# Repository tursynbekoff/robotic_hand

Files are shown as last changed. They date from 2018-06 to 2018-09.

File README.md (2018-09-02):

# Development of an Autonomous Robotic Pick and Place Laboratory Setup for Intelligent Industrial Automation
    
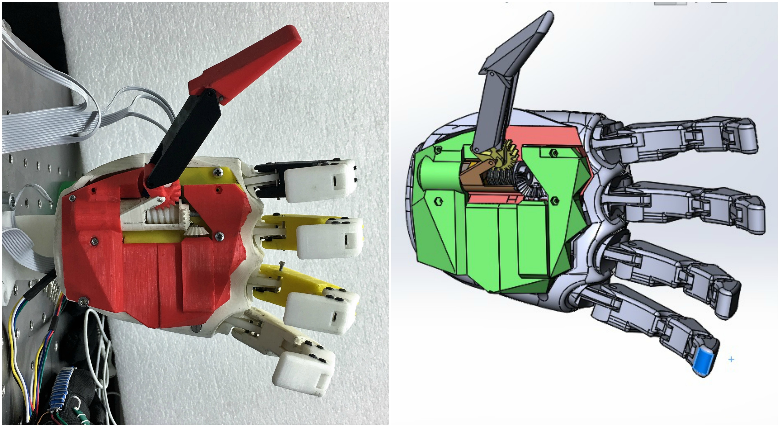
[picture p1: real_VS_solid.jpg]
 
The anthropomorphic hand consist of mechanical design and electrical components like 12V DC motor, arduino microcontroller wiring and PCB. In the following parts there will be full description of the mechanican and electrical components and source files could be found in the folders above

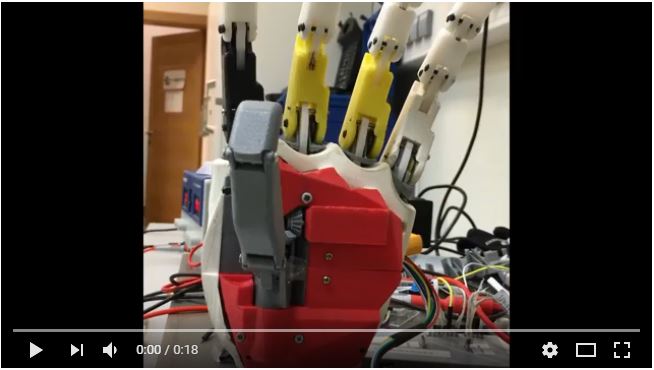
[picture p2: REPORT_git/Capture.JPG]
Video (https://youtu.be/M6sOJtzTVpo)


*  3D Design of the Hand 1.0
*  3D Design of the Hand 2.0
*  Control of the hand 

## 3D Design of the Hand 1.0
The robotic hand is still under iprovement and development stage. Here is shown previous models and developmemt steps that have been done. First model of the hand was done not by me and in a limited period of time. My goal is to improve design and eliminate problems from initial model. 

### Problems of the initial model
* Thumb was broken
* Backlash between parts 
* Wires were exposed to mechanical deformation
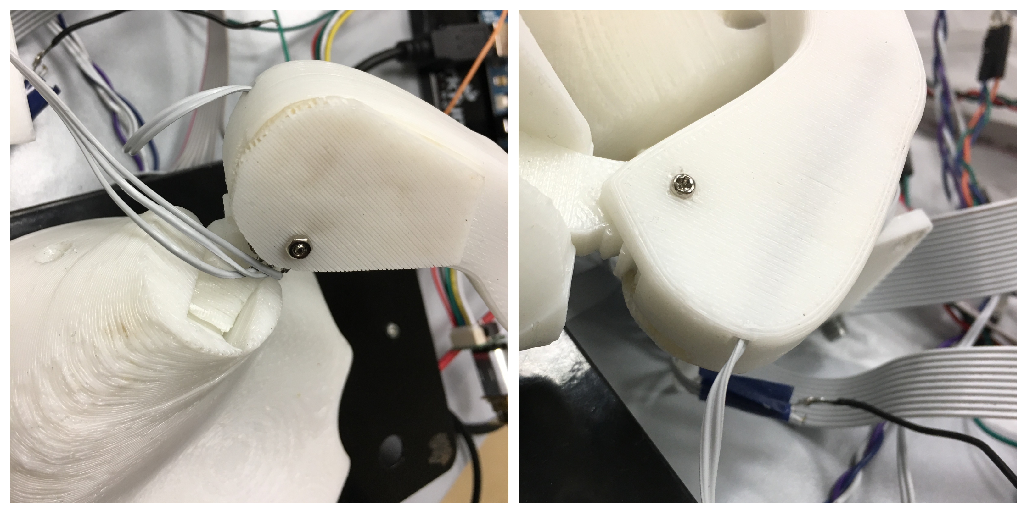
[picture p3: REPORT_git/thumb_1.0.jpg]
 
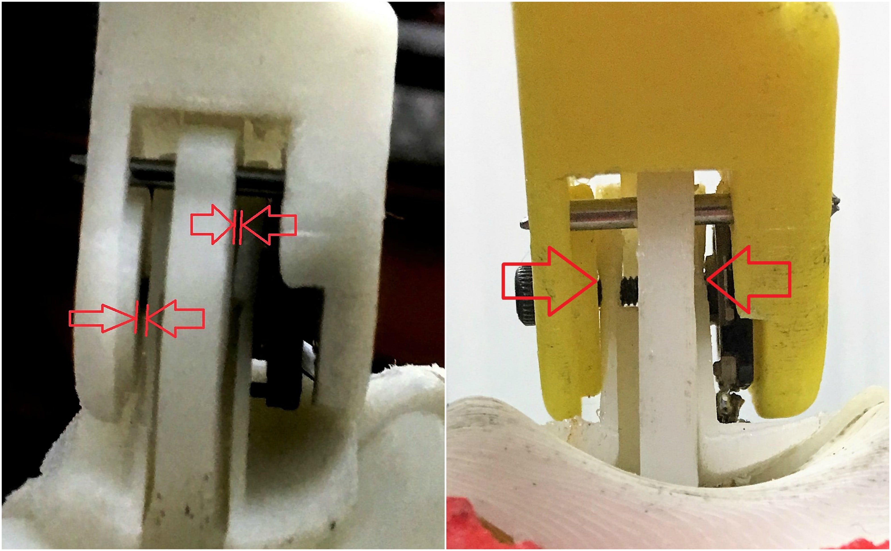
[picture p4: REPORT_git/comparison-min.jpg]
 
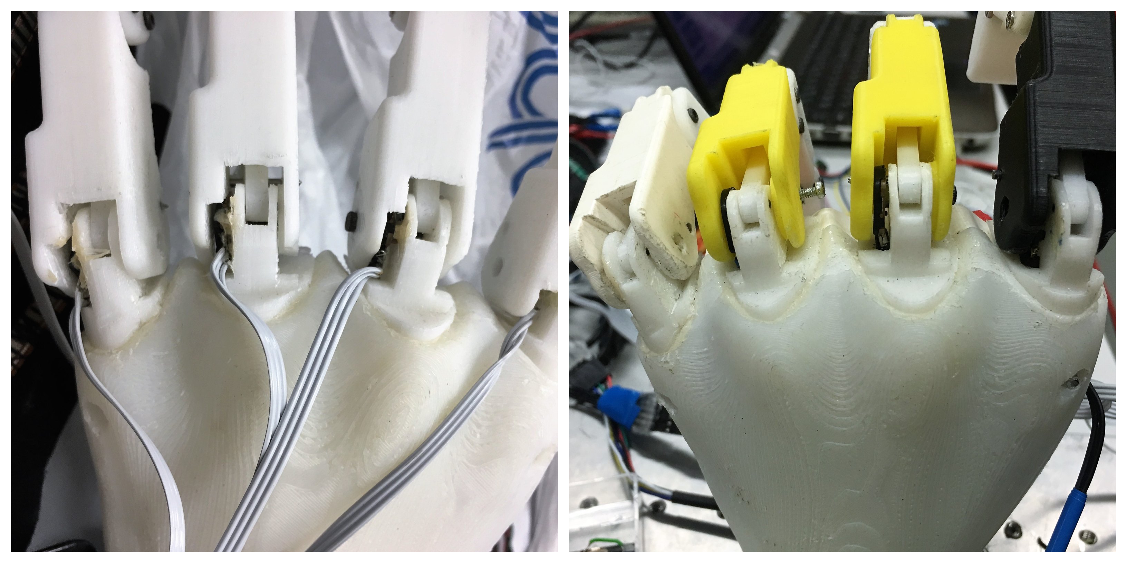
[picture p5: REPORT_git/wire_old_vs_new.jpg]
 
 
The problem with backlash was solved by replacing old parts with new ones. The new design of the "proximal phalanges" of the hand allowed to decrease backlash and the new placement of position sensors and location of the wiring of the sensors inside the hand improved sensor readings and precision of the hand. The advantage of placing position sensor inside the finger is straighforward, the data readings from sensor are cleaner and new placement also secures wiring from mechanical exposure.
### Setps of development of the new design of the thumb

The first picture demostrates initial design of the thumb

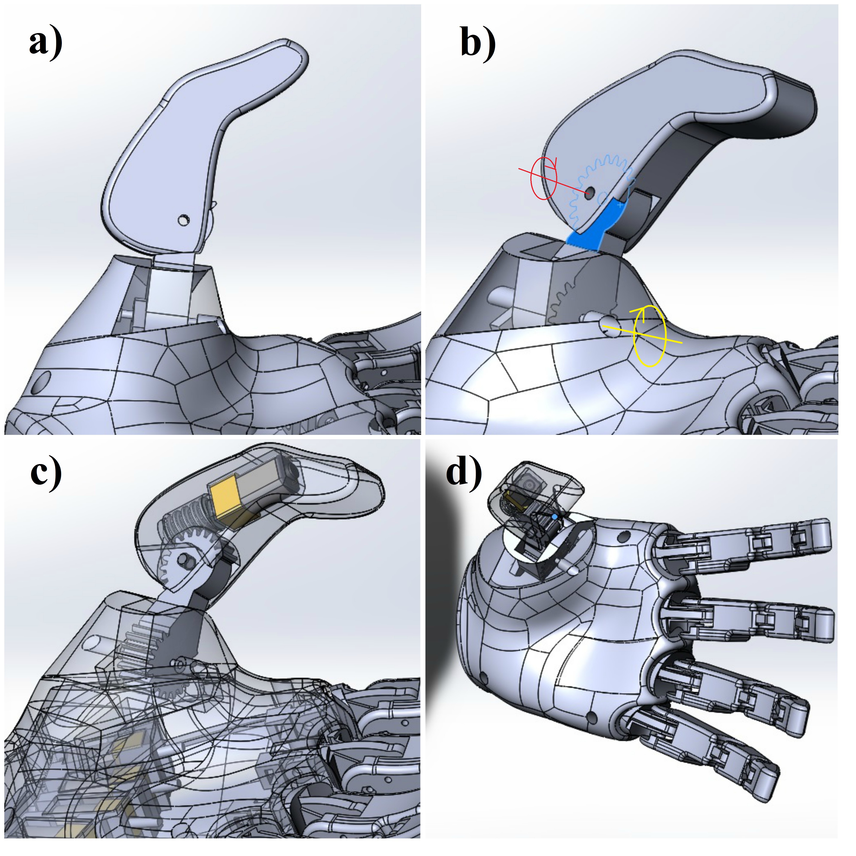
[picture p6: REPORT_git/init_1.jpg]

The first updated design of the thumb consisted from following configuration: flexion mechanism is performed with aid of brushed DC motor with integrated gearbox. The worm gear rotates spur gear which in turn performs extension, flexion movements. Moreover, the mechanism is non-backdrivable and performs in a positive way at grabbing operation it secures position even after power loss. In addition, thumb can perform underactuated adaptive closing through linkage connections. While extension, flexion operations thumb can bend depending on the placement of the object and wrap around that object. The second brushed DC motor rotates thumb with spur gear about its axis at "thumb's up" position. Thus, the thumb could perform only extension, flexion movements. However, the thumb in this configuration cannot perform abduction, adduction motions. As a result, the thumb cannot perform grabbing operation and further changes were made.

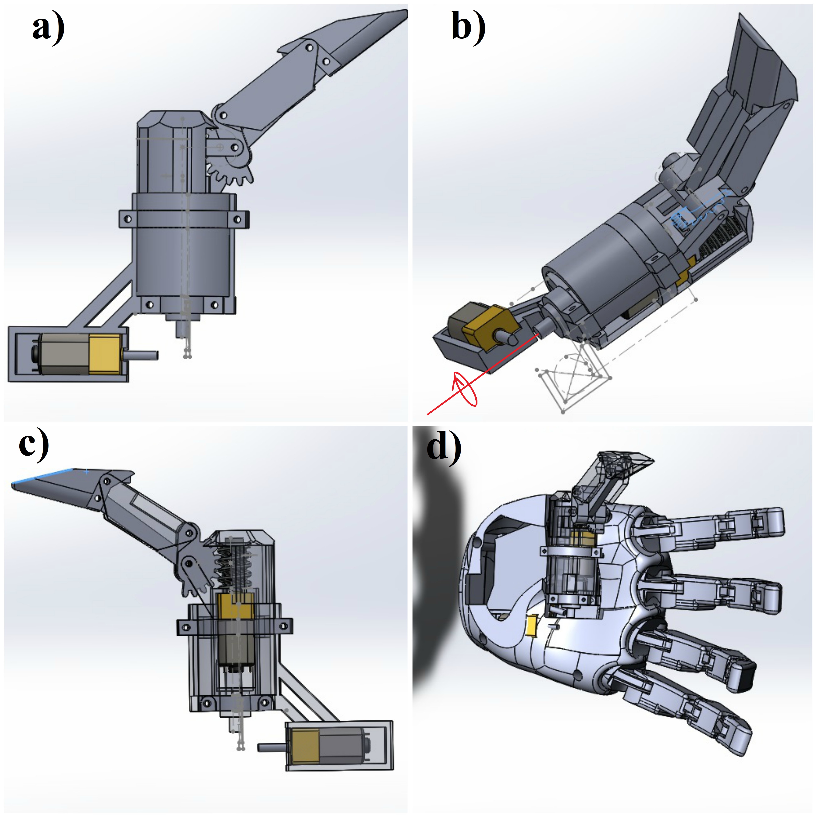
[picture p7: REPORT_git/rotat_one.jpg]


The second design of the thumb is different from initial design with the placement of the second brushed DC motor. Middle shaft were used to rotate thumb about palm plane. The thumb moves inward and outward from the palm plane, that means it can perform flexion, extension as well as abduction, adduction movements. However, this mechanism needs more space and eventually the design of the thumb were rebuilt.
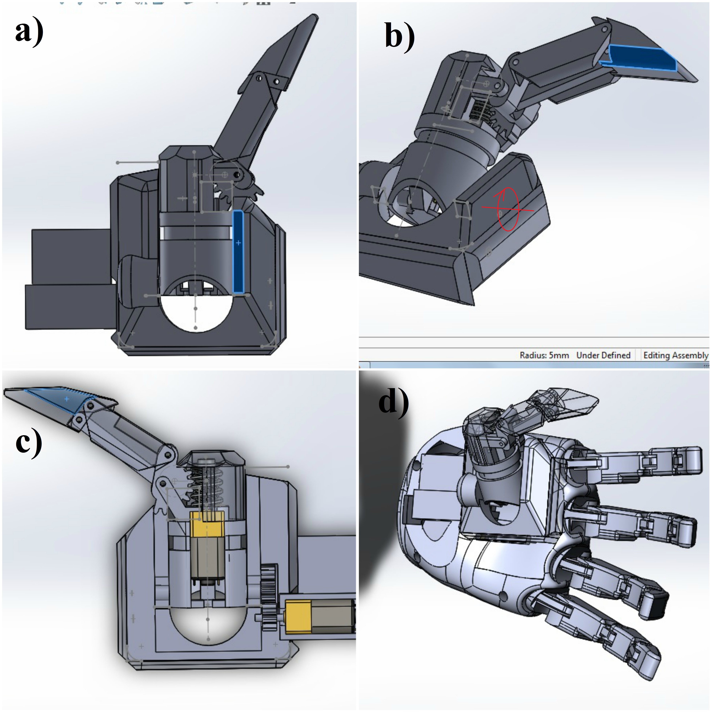
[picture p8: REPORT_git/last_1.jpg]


The next CAD model of the thumb can rotate about its base and can perform  flexion, extension and adduction. Placing the thumb opposite to index finger it can perform extension, flexion, abduction and adduction movements. In addition, this design does not need much space and can be compact in size. Space is needed only for DC motor. As a result, this CAD design is more effcient. The next design iterations  are fundamentally the same. The placement of the first DC motor is the same and adaptive mechanism is rotated to 90 degrees and placed opposite to index finger. The second brushed DC motor rotates the thumb around index finger axis by using bevel gear. The advantage using bevel gear instead of spur gear, it conserves space. As a result, we started printing the parts.

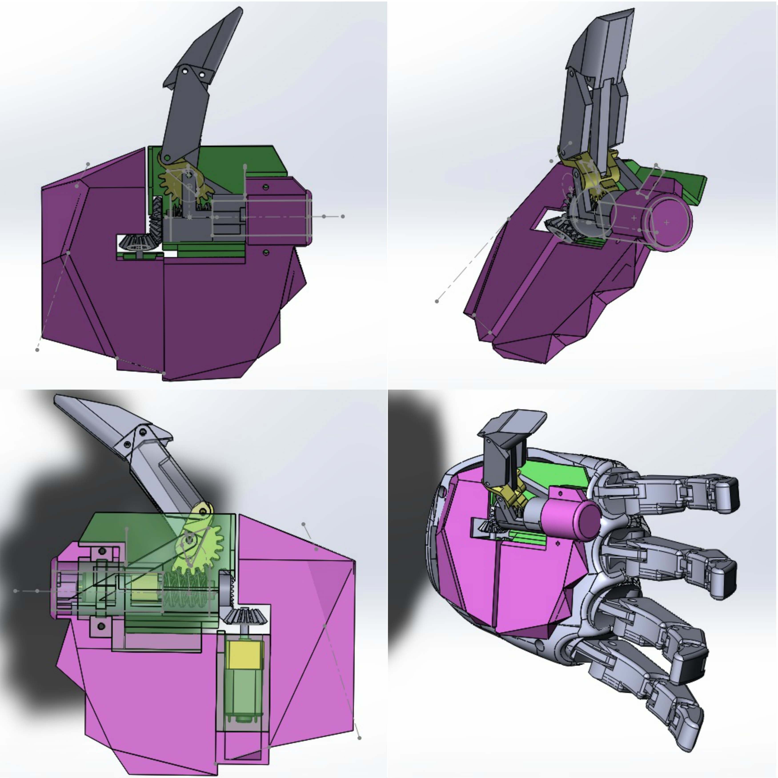
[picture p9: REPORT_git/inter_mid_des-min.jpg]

 
The last design: 

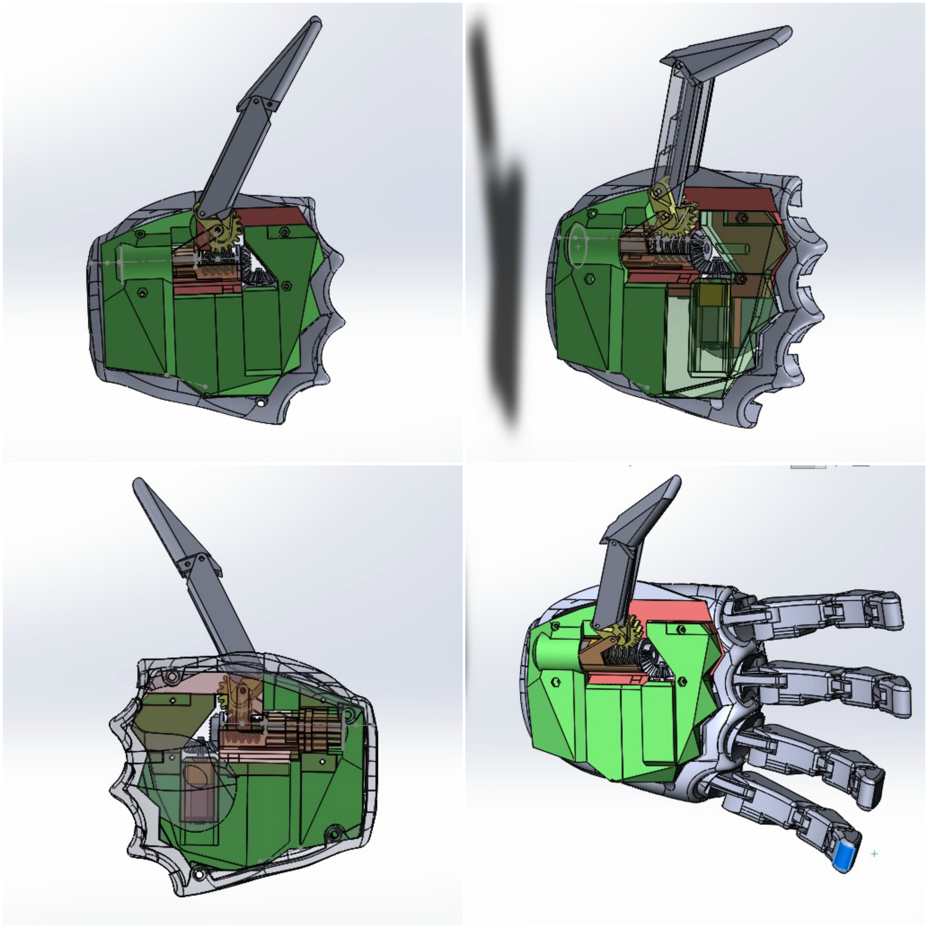
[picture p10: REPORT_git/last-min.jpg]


The next iteration was connection of mechanical part with electrical components. Due to dynamic configuration of the thumb and moving mechanical structures of the hand it created diffculties with wiring. DC motors, that were used in the project, has embedded quadratic encoders, therefore each motor has six pins to connect. The first DC motor is integrated in the moving structure that rotates around its axis. The second DC motor rotates the structure with the first DC motor. The requirement for the harness is flexibility and transmitting rated power for the motor. As a result, the wiring loom was made from copper wires that widely used in headphones. In addition, mechanical changes were made for harness wiring, it goes through narrow slot in the moving part and protected from mechanical deformation. However, the part of the wire harness which connects dynamic part with static part is exposed to bending. To secure robustness of the exposed part of the harness, insulating tape was used. 

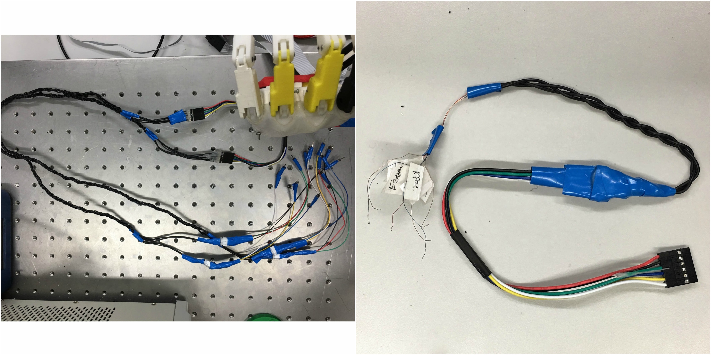
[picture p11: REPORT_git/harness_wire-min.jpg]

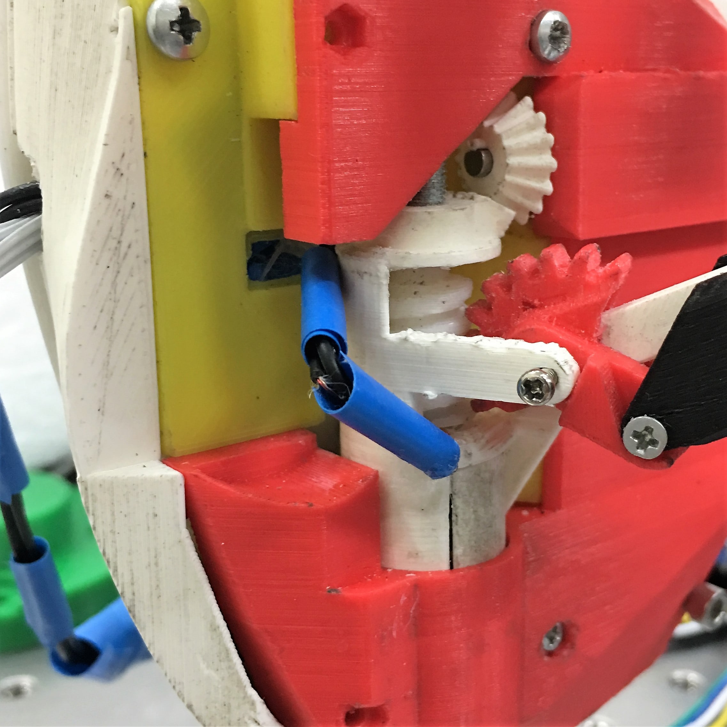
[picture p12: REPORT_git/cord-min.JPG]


As a result, the final CAD model of the thumb can perform extension, flexion and abduction, adduction movements. The main difference between initial and the final model of the thumb, it can perform under-actuated adaptive motion, which means the thumb can wrap around object with complex geometrical shape and simplifies the control of the thumb. Full up-to-date CAD model of the hand is [here](https://github.com/tursynbekoff/robotic_hand/tree/master/CAD).

### Holding objects

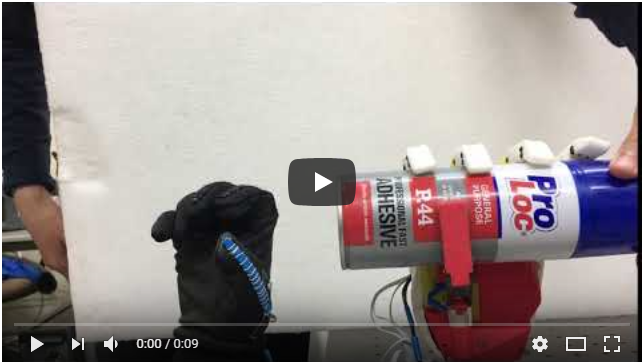
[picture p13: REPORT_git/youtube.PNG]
IMAGE ALT TEXT HERE (https://youtu.be/hmZBOrk-Xx8)


The performance of the hand with new thumb was tested with various objects. In the test
there were objects with different shapes: cylindrical, spherical and brick shaped. The hand
performed grabbing with aid of manual manipulation. The hand securely holds all objects and thumb performs adaptive gripping of the objects. Underactuated adaptive bending of the thumb helps to grab and to hold objects. However, the length and the shape of the thumb should be tuned for versatility. The grip of the thumb can be improved by adding nonbackdivable mechanism where bevel gear is placed. Other possible way to improve the grip, by resin coating on the contact point with the object, on the inner surface of the thumb.

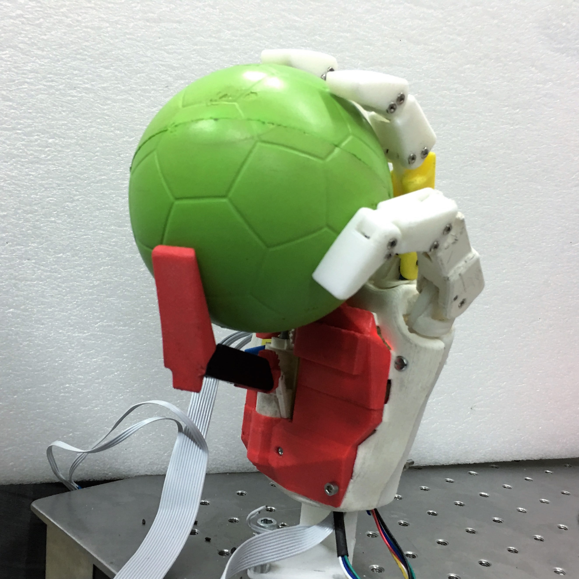
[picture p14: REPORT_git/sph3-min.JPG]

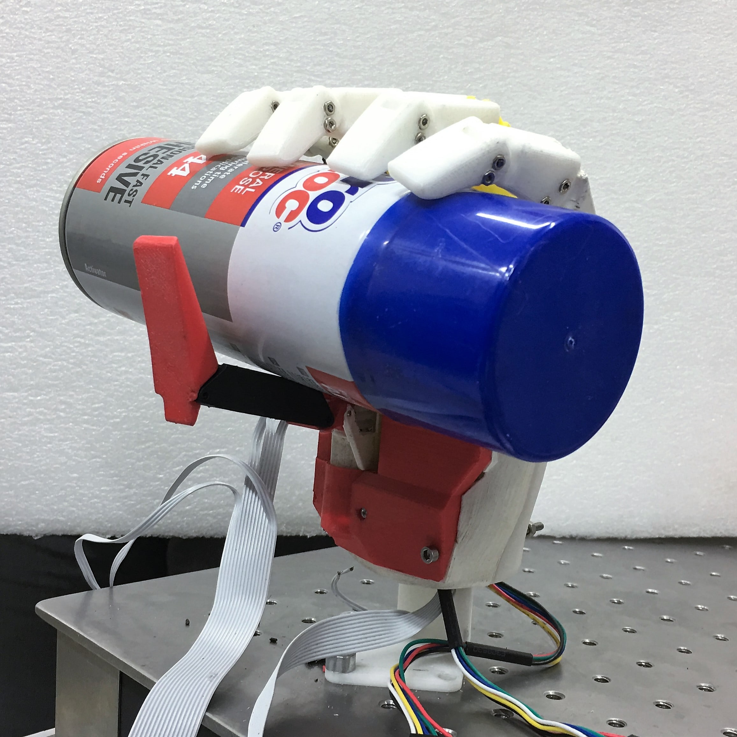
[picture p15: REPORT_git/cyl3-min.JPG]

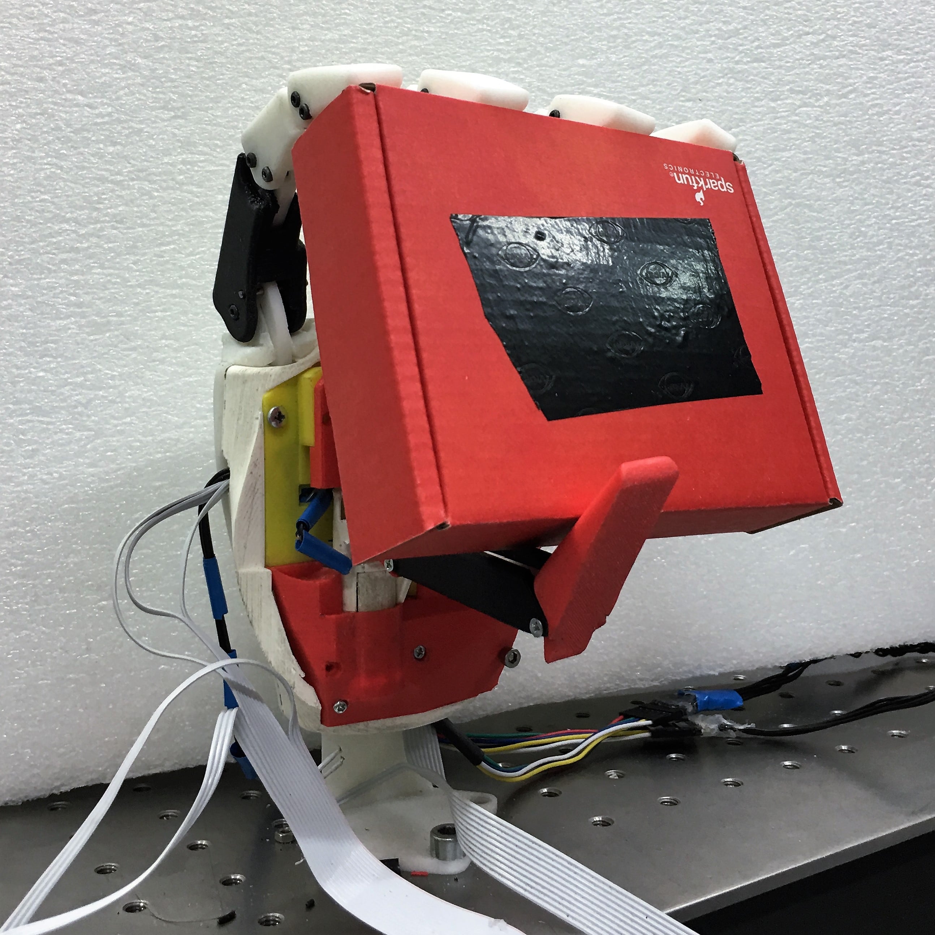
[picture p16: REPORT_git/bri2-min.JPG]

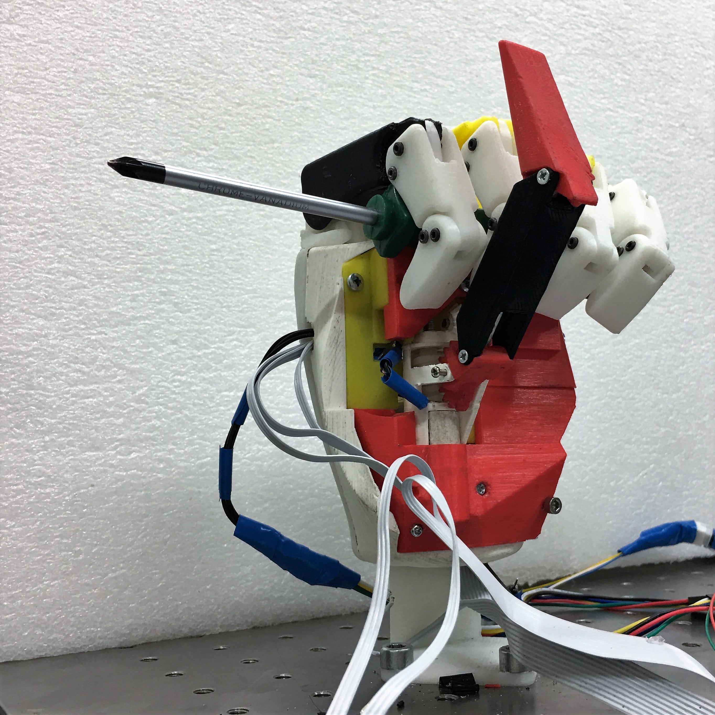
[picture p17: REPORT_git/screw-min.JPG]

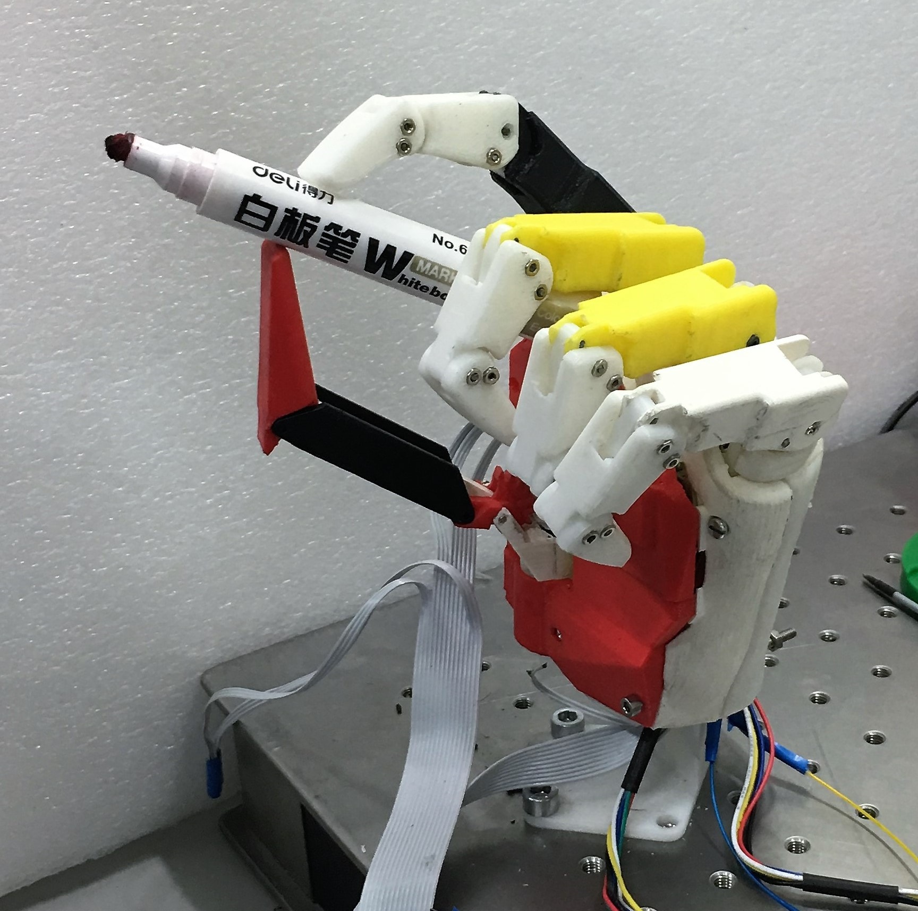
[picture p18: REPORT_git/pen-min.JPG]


In addition, household objects with complex geometrical configuration, as screwdriver, were tested. The hand can grab the objects with external manipulation and securely hold objects at specific position. The hand has potential to be used as prosthesis.

## Hand 2.0
### New Finger Mechanism
currently working on adaptive underactuated mechanism for fingers

Demo
CAD files for finger are [here](https://github.com/tursynbekoff/robotic_hand/tree/master/test_finger)

Demo

New hand with rail sysem for stablitity and robustness is under integration process.
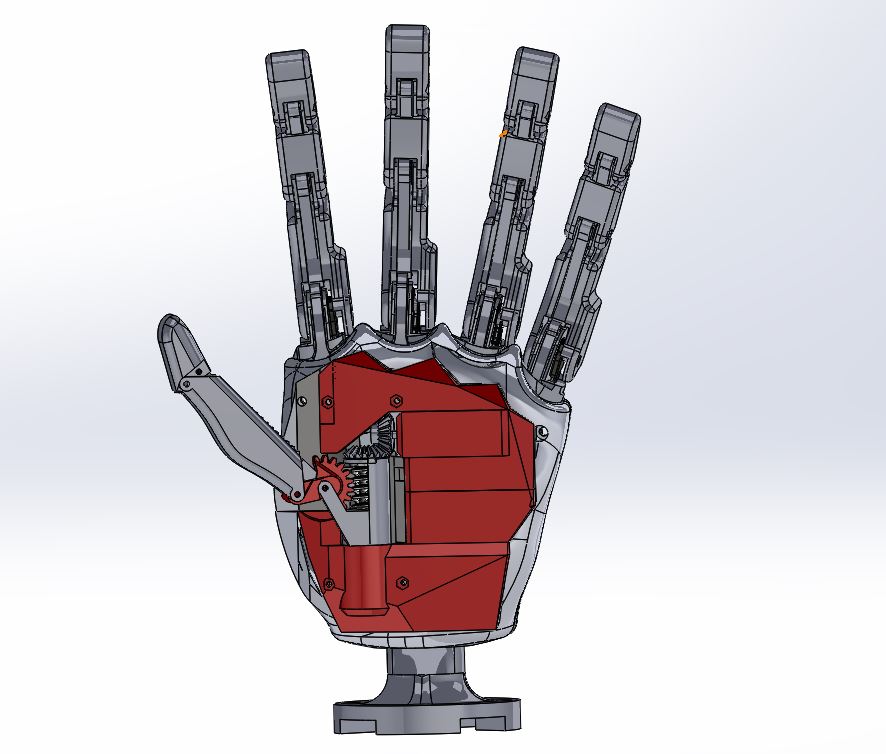
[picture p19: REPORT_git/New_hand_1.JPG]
New hand

The crossed structures are used for stiffness and strength to hold rails stable. Rails are used to navigate motor joint part durring mechanical transition from rotational motion to linear motion. Earlier there was no rail system and there were parisite vibration in rotaional motion which created disturbance in postion sensor readings. From the first tests fingers move in defined trajectory. 
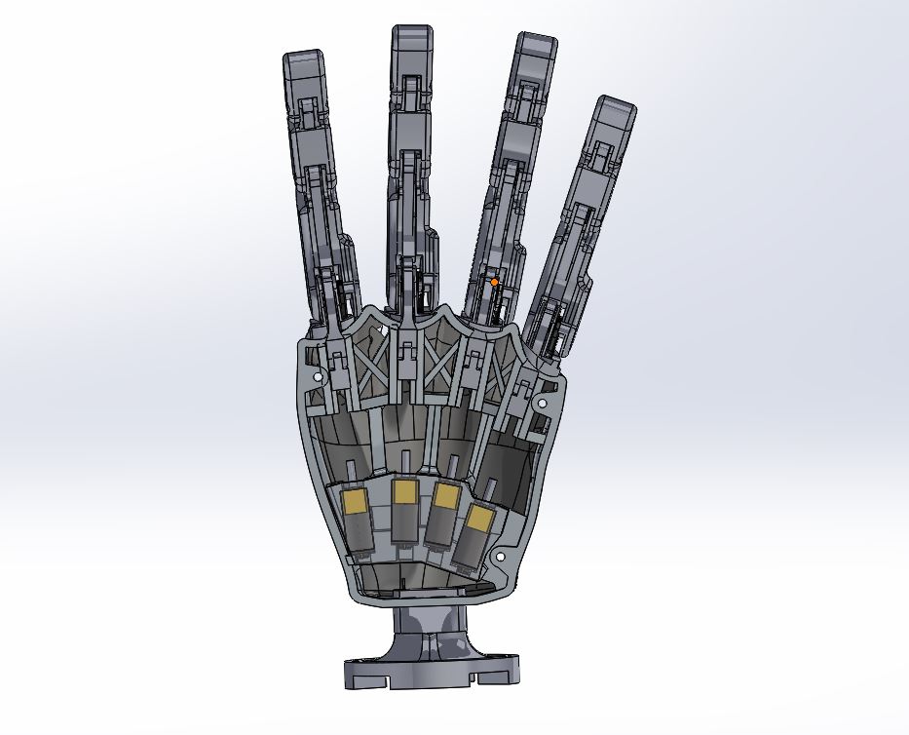
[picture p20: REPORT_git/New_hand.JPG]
New hand


## Control of the hand

All fingers of the hand equipped with encoders: 2 quadrature encoders for thumb and position sensor for other fingers. This is necessary to receive position feedback and avoid critical points, that can destroy finger structure and motor. There are six brushless DC motors that require dual motor drivers (DRV8835). For dual motor driver, 4 motor control signals (2 signal per motor) is sent from Arduino. The signal to the motors must be PWM, while the other zero to move in one direct, the opposite to move in reverse direction. If both signals are zero, motor stops. Apart from that, 10V with 1A power is connected to Vcc that is supplied to the motors. Initially all the electrical components were connected to the breadbord. Breadbord caused many hardware problems with robustness of the system. As a result, the idea of creating PCB was in demand. PCB was designed in CicuitMaker(open source free software). New PCB eliminates potential hardware failures and serves as a 6-channel Arduino motor shield and I/O for digital and analog pins. In addition, to secure from environment and potential mechanical failure, housing was developed and files for housing could be found in the folder [Housing](https://github.com/tursynbekoff/robotic_hand/tree/master/Housing).
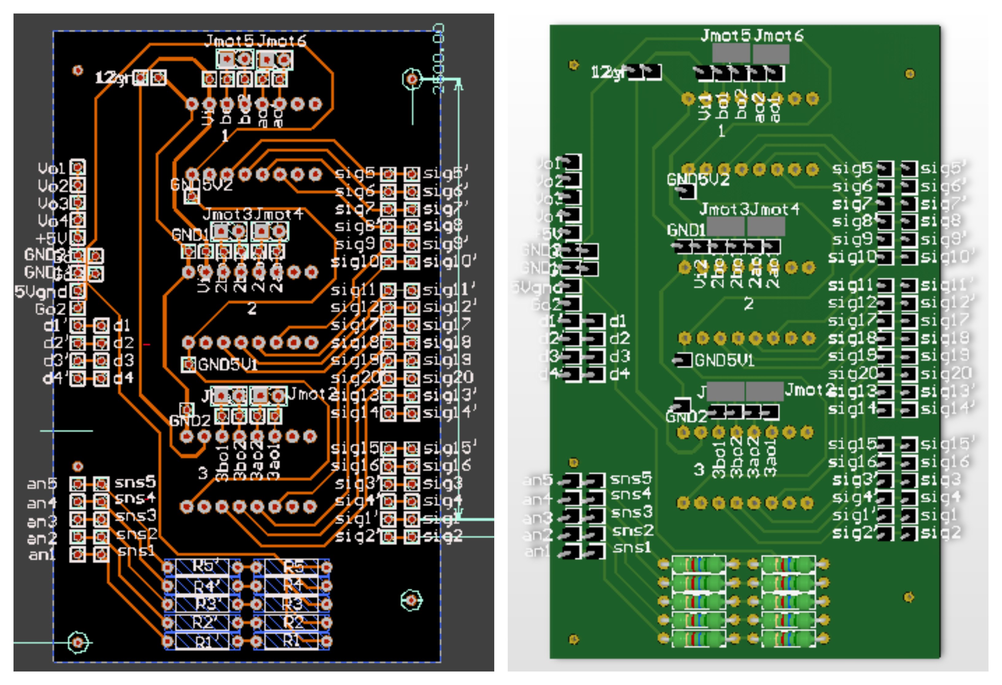
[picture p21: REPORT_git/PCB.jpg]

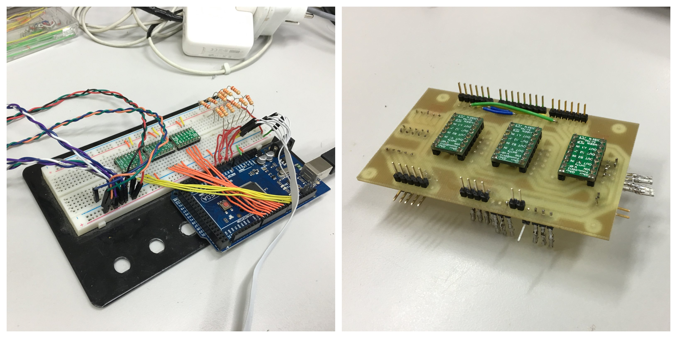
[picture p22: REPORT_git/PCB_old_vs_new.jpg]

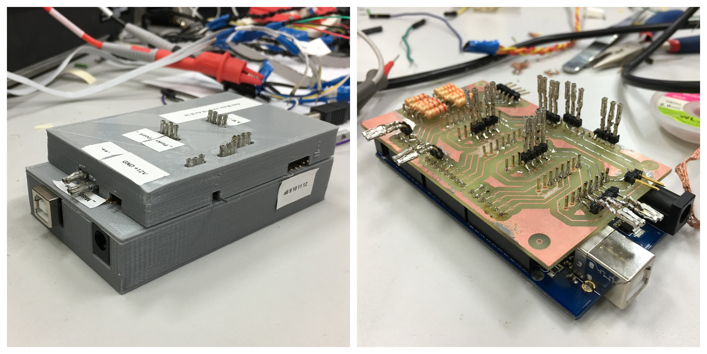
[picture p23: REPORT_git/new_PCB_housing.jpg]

Full **PCB** design could be found from the following [link](https://circuitmaker.com/Projects/Details/Talgat-Tursynbekov/Robotic-hand). Full **script** for hand controll is [here](https://github.com/tursynbekoff/robotic_hand/tree/master/Control/hand_control_1.0).

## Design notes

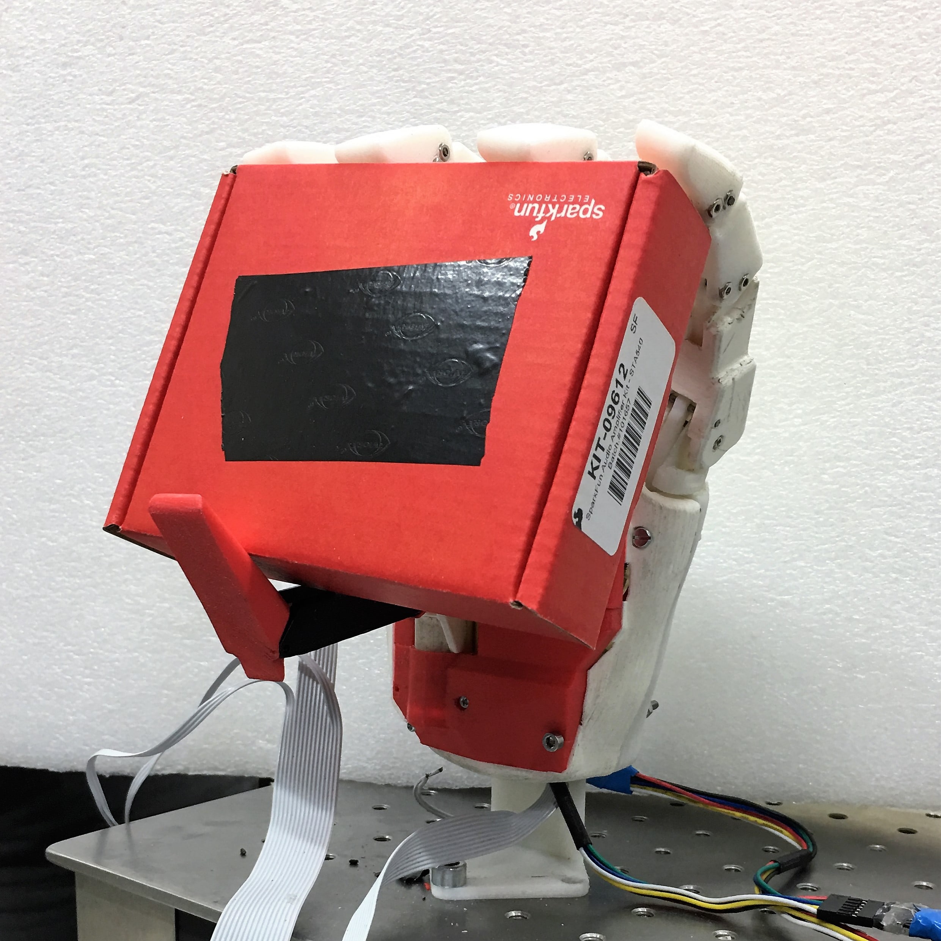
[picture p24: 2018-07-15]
REPORT_git/bri3-min.JPG

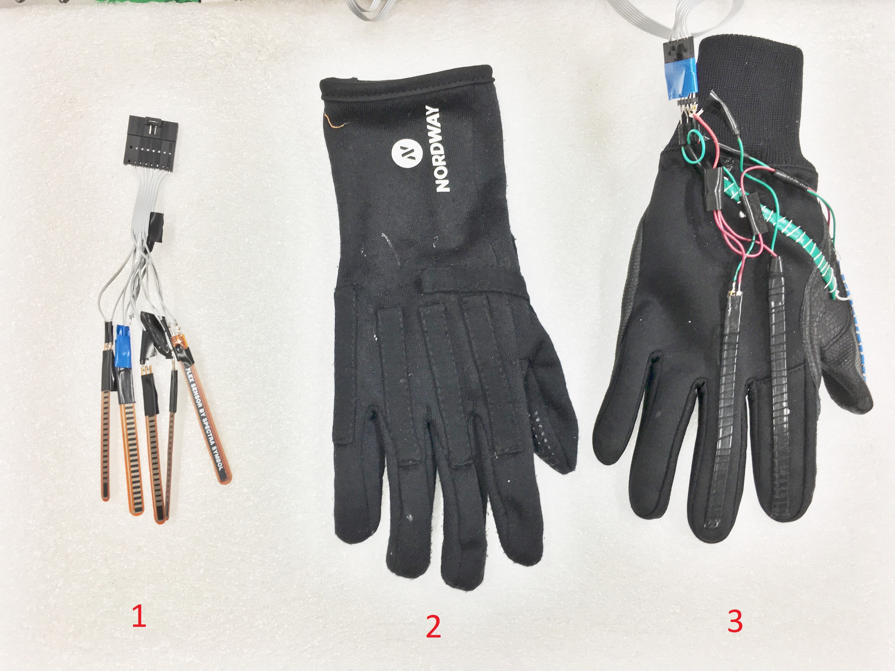
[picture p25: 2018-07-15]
REPORT_git/glove-min.JPG

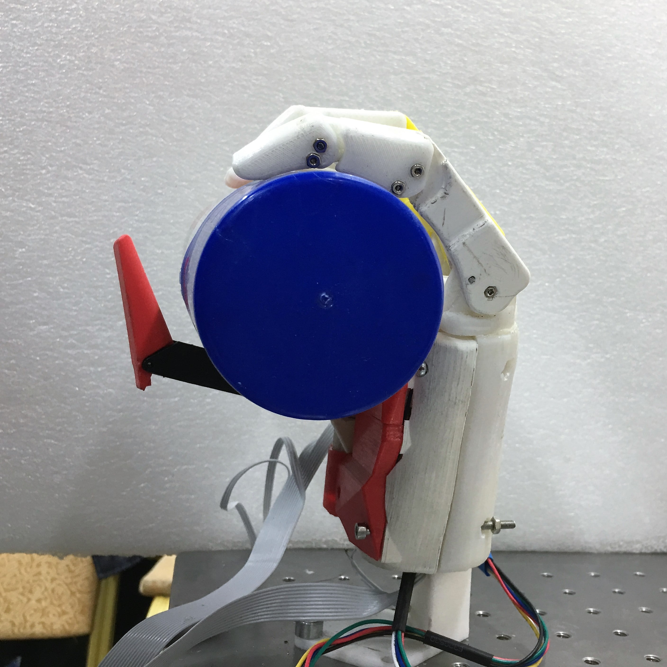
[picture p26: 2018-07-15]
REPORT_git/cyl4-min.JPG

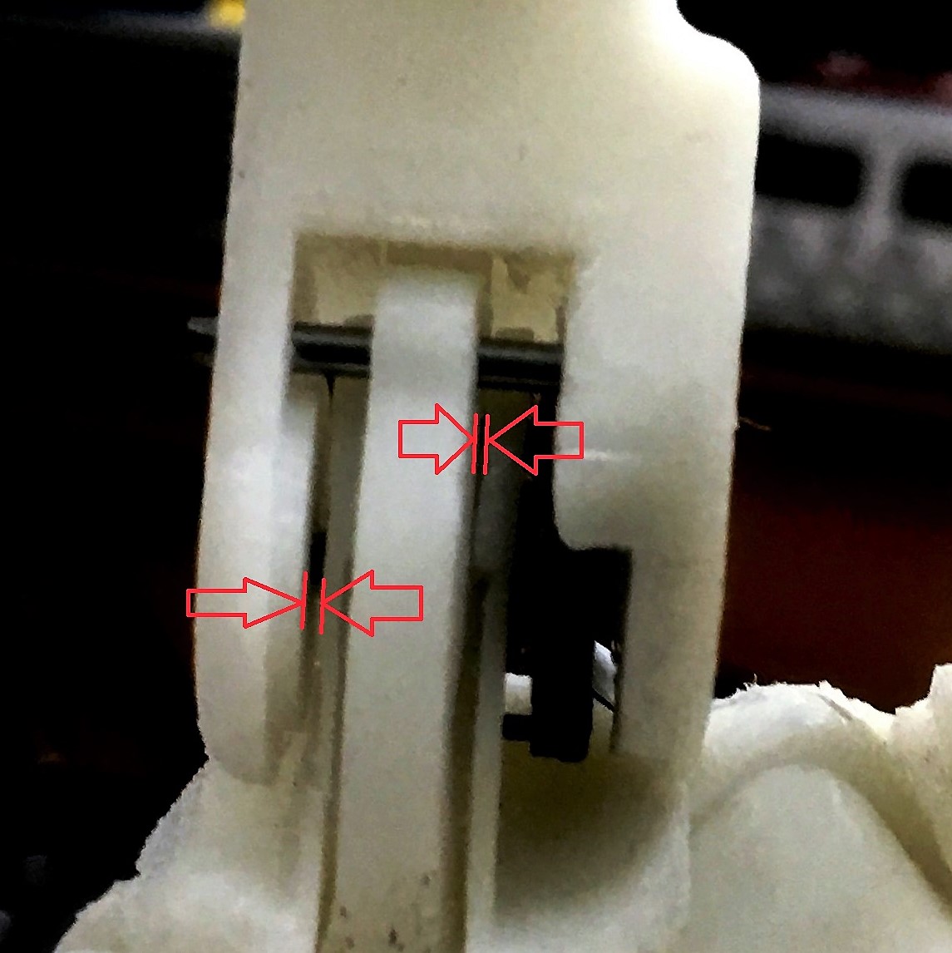
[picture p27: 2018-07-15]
REPORT_git/backlash.jpg

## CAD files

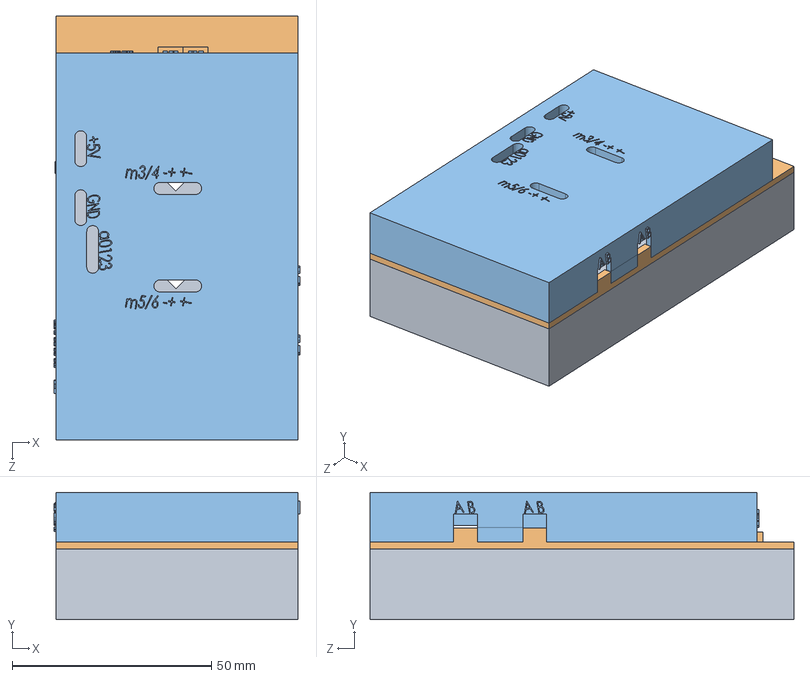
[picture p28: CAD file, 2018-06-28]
Housing/Assem1.SLDASM
61.8 x 32.0 x 106.5 mm

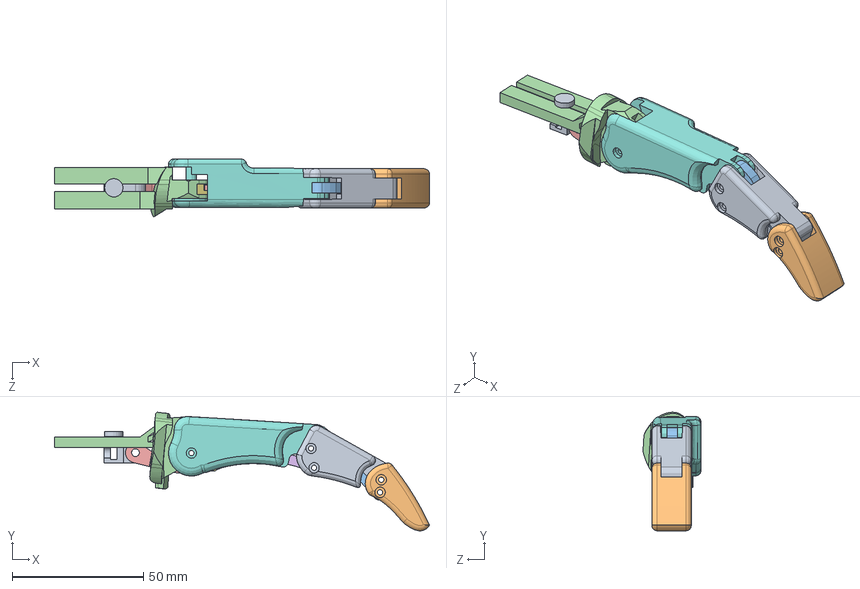
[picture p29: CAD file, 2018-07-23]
test_finger/Assem2.SLDASM
142.7 x 45.1 x 22.1 mm
Link 1
Finger Base
Set screw Link 1
Part1^Assem2
Part2^Assem2
motor Link2

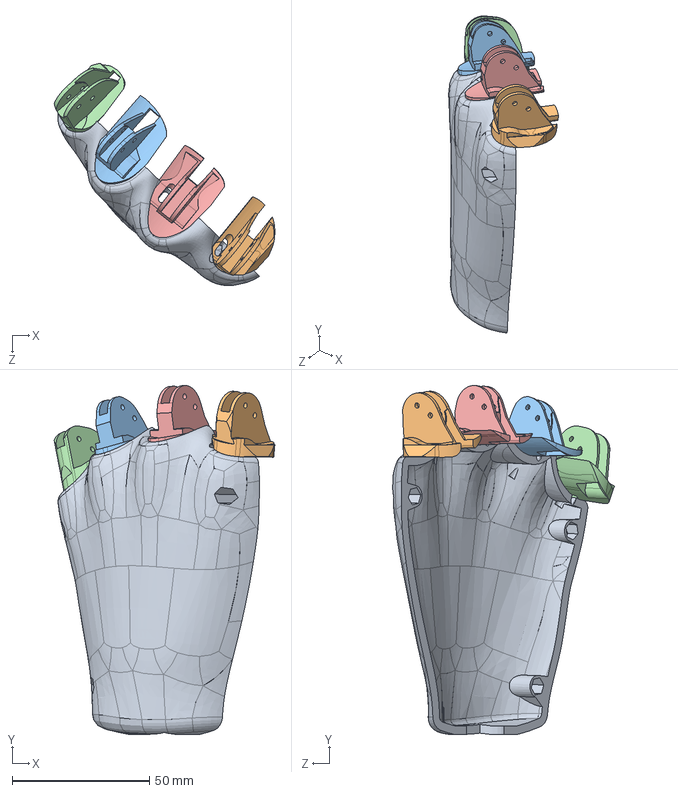
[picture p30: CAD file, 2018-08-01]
CAD/HAND_back/Back_hand.SLDASM
80.4 x 127.2 x 80.9 mm
TestPalm1.1h2
Finger Base
Finger Base2
Finger Base3
Finger Base1

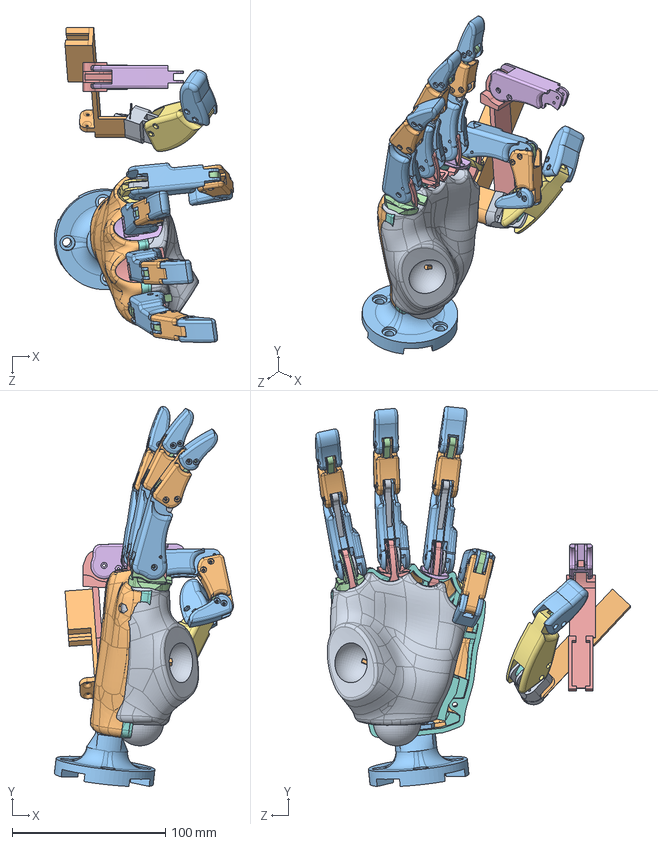
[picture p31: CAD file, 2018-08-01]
CAD/HAND_back/Assem1.SLDASM
117.0 x 248.0 x 205.4 mm
Link 2 x 4
Link 1 x 4
Finger Base
Finger Base1
Finger Base2
Finger Base3
TestPalm1
298,1 Micro Metal Gearmotor MP x 4
motor Link2 x 4
Motor Lnik test x 4
Lid for palm motors
p_sensor x 4
TestPalm1.1h2
Eperimental Base

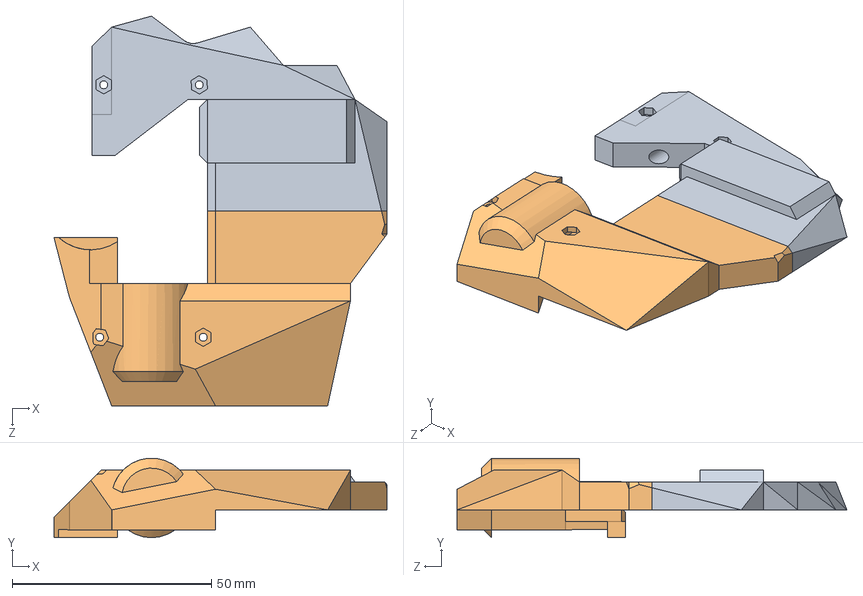
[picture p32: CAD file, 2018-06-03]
CAD/Thumb_2.1.SLDASM
83.7 x 20.0 x 97.9 mm
cover5_1
cover5_2

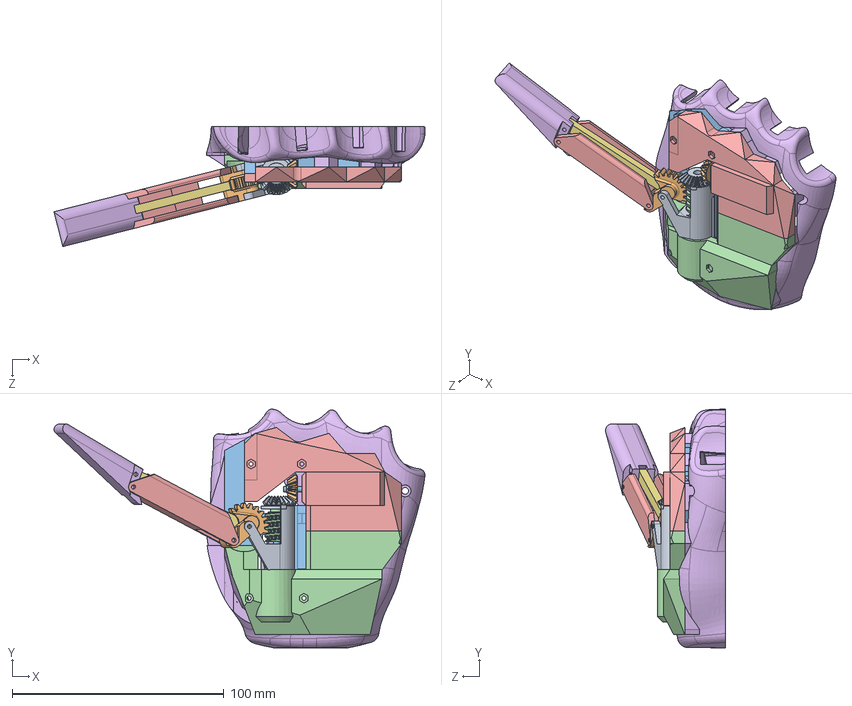
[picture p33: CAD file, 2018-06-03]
CAD/Thumb_2.0.SLDASM
175.3 x 112.9 x 56.7 mm
THUMB_Base1
THUMB_5.1
Worm Module 1 short pin version
THUMB_4.1
THUMB_1.1tip
THUMB_1.1link1
cover4
24_teeth
13_teeth
cover6
298,1 Micro Metal Gearmotor MP
cover5_2
cover5_1
TestPalm2

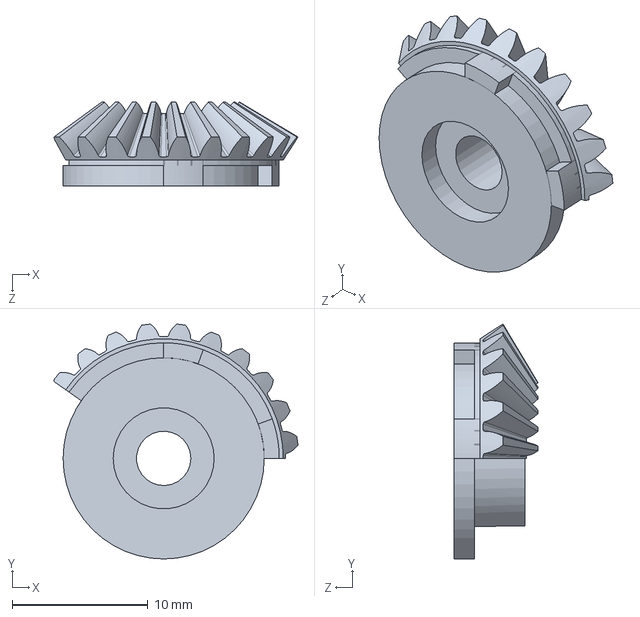
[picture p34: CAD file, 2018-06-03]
CAD/24_teeth.SLDPRT
18.0 x 17.3 x 6.15 mm

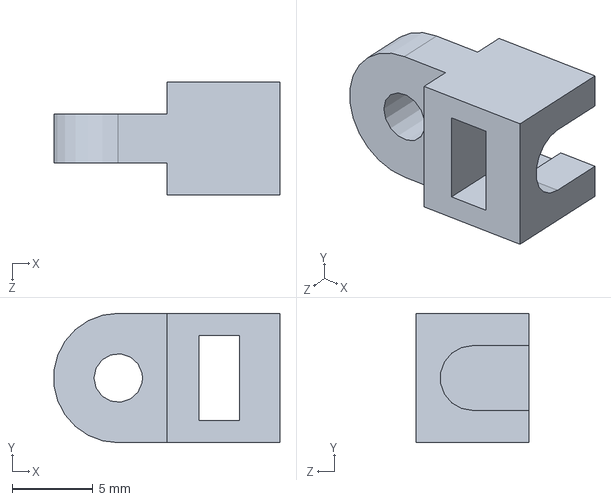
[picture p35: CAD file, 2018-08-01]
CAD/HAND_back/motor Link2.SLDPRT
14.0 x 8.00 x 7.00 mm

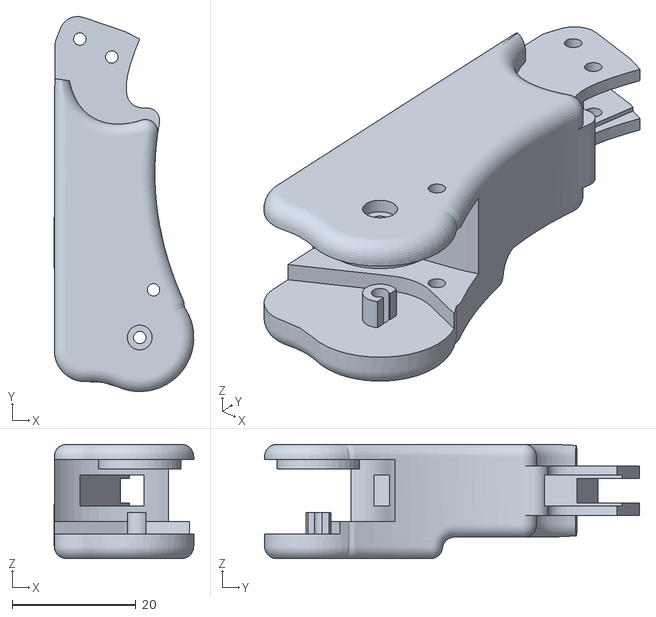
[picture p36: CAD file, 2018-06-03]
CAD/Новая папка/Part 3 (1)_1.STL
22.5 x 60.6 x 18.5

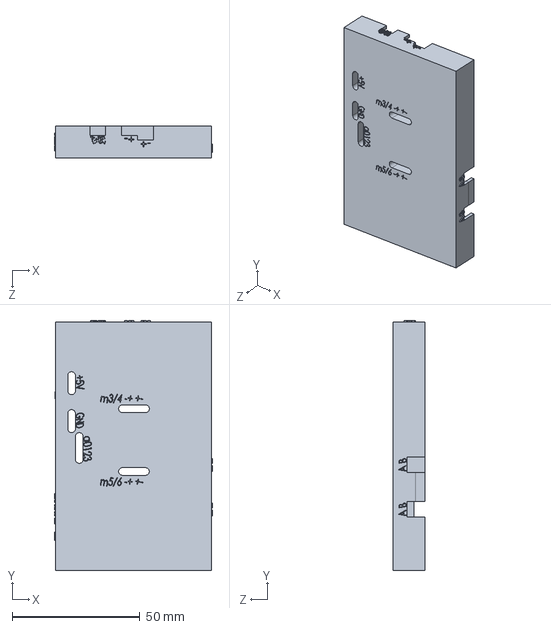
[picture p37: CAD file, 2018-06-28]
Housing/Part4.sldprt
61.8 x 97.7 x 12.5 mm

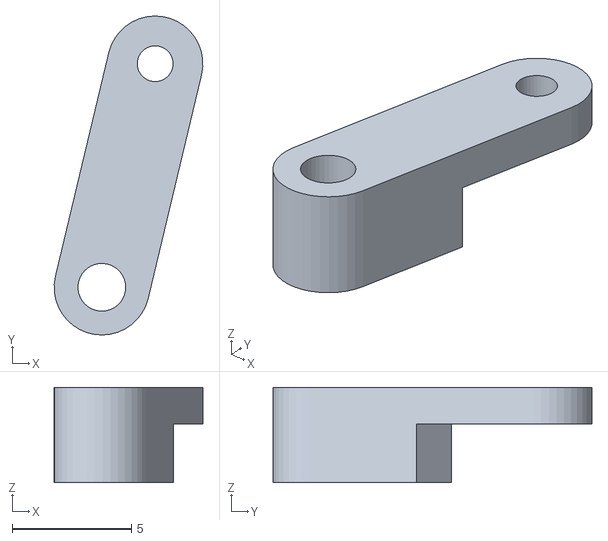
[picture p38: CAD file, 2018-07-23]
test_finger/STL/Part2^Assem2.STL
6.23 x 13.4 x 4.00

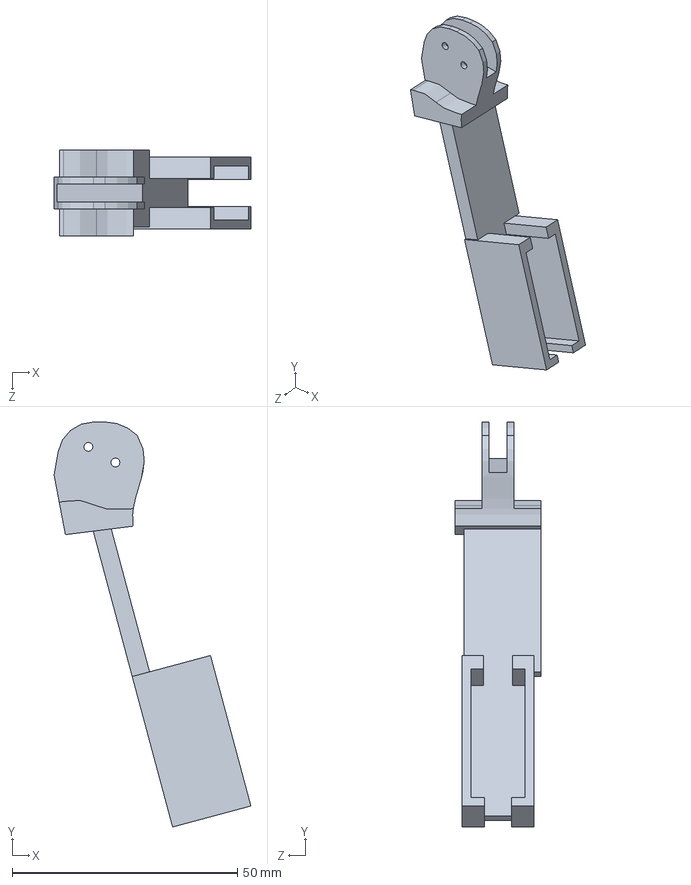
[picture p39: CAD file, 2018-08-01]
CAD/HAND_back/Part 4.SLDPRT
43.7 x 89.9 x 19.0 mm

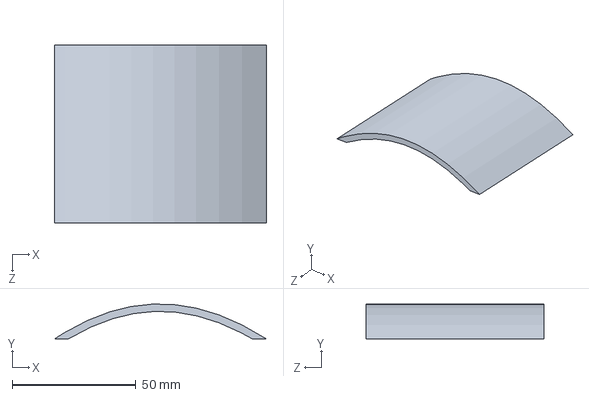
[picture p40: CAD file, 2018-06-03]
CAD/Palm.SLDPRT
85.8 x 14.1 x 72.0 mm

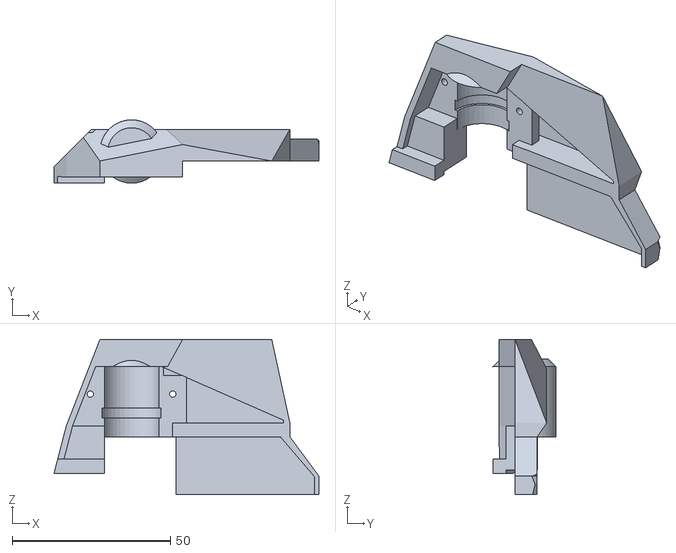
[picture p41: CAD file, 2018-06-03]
CAD/Новая папка/THUMB_5.1.STL
83.7 x 20.0 x 49.0

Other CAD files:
Housing/Part1.SLDPRT
test_finger/STL/Part1^Assem2.STL
CAD/HAND_back/Thumb motor base2.SLDPRT
CAD/Новая папка/Bevel Gear.STL
CAD/1 DOF Thumb.SLDPRT
CAD/12teeth.SLDPRT
CAD/13_teeth.SLDPRT
CAD/24teeth.SLDPRT
CAD/298,1 Micro Metal Gearmotor MP.SLDPRT
CAD/Base.SLDPRT
CAD/Eperimental Base.SLDPRT
CAD/Finger Base.SLDPRT
CAD/Finger Base1.SLDPRT
CAD/Finger Base2.SLDPRT
CAD/Finger Base3.SLDPRT
CAD/Gear 16T.SLDPRT
CAD/Gear 34T.SLDPRT
CAD/HAND_back/298,1 Micro Metal Gearmotor MP.SLDPRT
CAD/HAND_back/Back_hand.SLDPRT
CAD/HAND_back/Back_hand_2.SLDPRT
CAD/HAND_back/Eperimental Base.SLDPRT
CAD/HAND_back/Finger Base.SLDPRT
CAD/HAND_back/Finger Base1.SLDPRT
CAD/HAND_back/Finger Base2.SLDPRT
CAD/HAND_back/Finger Base3.SLDPRT
CAD/HAND_back/Hex Stand off 1 inch.SLDPRT
CAD/HAND_back/Lid for palm motors.SLDPRT
CAD/HAND_back/Link 1.SLDPRT
CAD/HAND_back/Link 2.SLDPRT
CAD/HAND_back/Motor Lnik test.SLDPRT
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

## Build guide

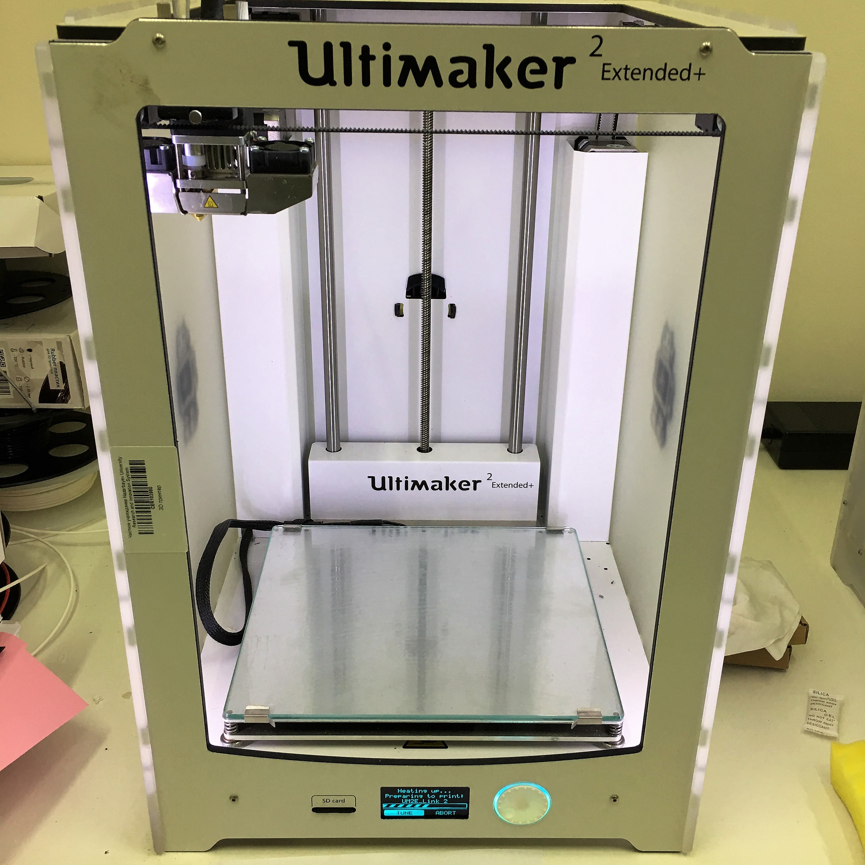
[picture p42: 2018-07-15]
REPORT_git/3D printer-min.JPG

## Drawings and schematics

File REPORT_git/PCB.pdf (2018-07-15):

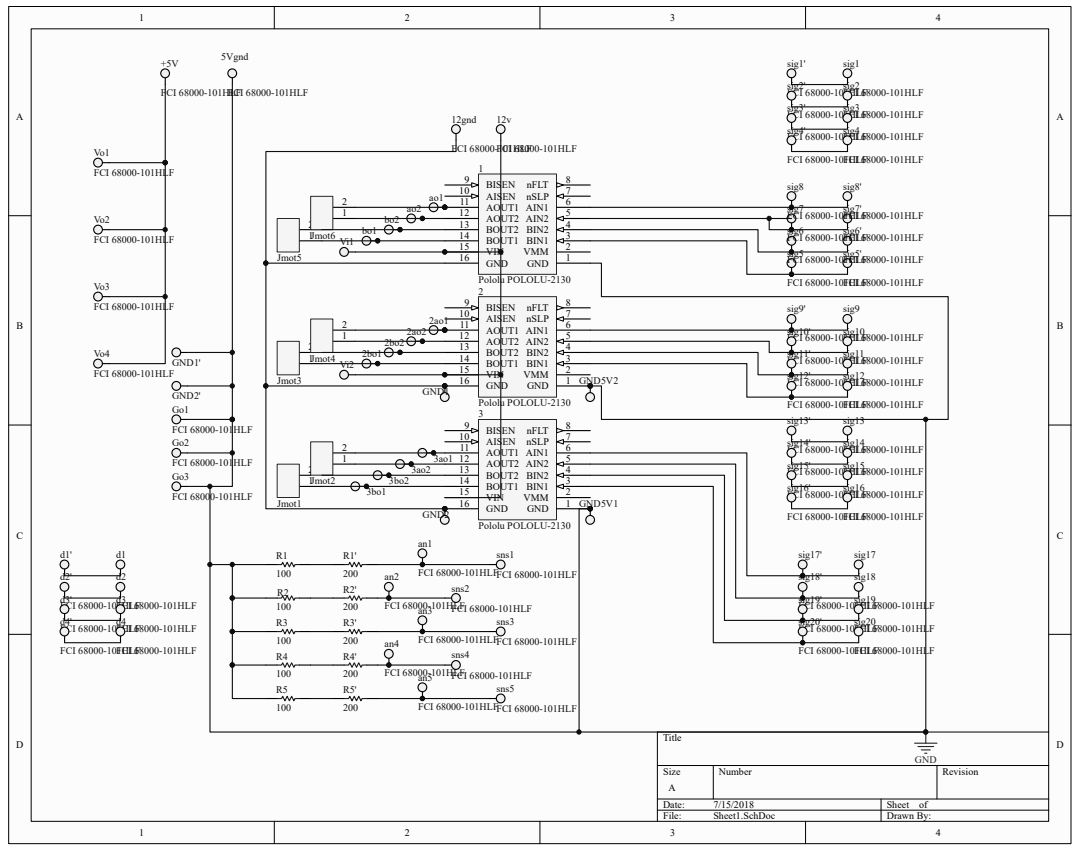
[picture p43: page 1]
Title; Size; Number; Revision; Date:; Sheet of; File:; Sheet1.SchDoc; Drawn By:; GND; VMM; BIN1; BIN2; AIN2; AIN1; nSLP; nFLT; 8 BISEN 9; AISEN 10 AOUT1 11 AOUT2 12 BOUT2 13 BOUT1 14 VIN 15 GND 16; Pololu POLOLU-2130; FCI 68000-101HLF an2; FCI 68000-101HLF an3; FCI 68000-101HLF an4; FCI 68000-101HLF an5; FCI 68000-101HLF; sns1; sns2; FCI 68000-101HLF sns3; sns4; FCI 68000-101HLF sns5; 5Vgnd; 12gnd; sig1; sig1'; FCI 68000-101HLF sig2; sig2'; FCI 68000-101HLF sig3; sig3'; FCI 68000-101HLF sig4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

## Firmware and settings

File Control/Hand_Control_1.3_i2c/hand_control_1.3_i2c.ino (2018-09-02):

#include <Wire.h>

unsigned long x = 0;
//#include <PID_v1.h>
int sensorPin1 = A1;    // Point finger
int sensorPin2 = A2;    // Middle finger 
int sensorPin3 = A0;    // Ring finger

//double Kp=0, Ki=10, Kd=0;
//PID myPID(&Input, &Output, &Setpoint, Kp, Ki, Kd, DIRECT);
int i=0;
int rotateVal = 40;

int encoder0PinA = 19;
int encoder0PinB = 18;
//int encoder0Pos = 0;
int encoder0PinALast = LOW;
int n0 = LOW;
//long pos0 = 0;

int encoder1PinA = 21;
int encoder1PinB = 20;
//int encoder1Pos = 0;
int encoder1PinALast = LOW;
int n1 = LOW;
//long pos1 = 0;

long encoder1PosR = 0;
long encoder0PosR = 0;

int encoder0PinALastR = 0;
int encoder1PinALastR = 0;

int y;
int r;
unsigned long serialData;
int inbyte; 
int digitalState;
int pinNumber;
int analogRate;

int sensorVal1;
int sensorVal2;
int sensorVal3;

int rotateVal1 = 120;
int rotateVal2 = 120;
int rotateVal3 = 120;
int rotateVal4;
int rotateVal5;

int sensorVal7;
int sensorVal8;
int sensorVal9;

int rotateVal7;
int rotateVal8;
int rotateVal9;
int mot1p = 7;       // Motor 1  POINT  OPENING  sensor 1
int mot1m = 6;       //                 CLOSING

int mot2p = 13;      // Motor 2 MIDDLE  OPENING  sensor 2
int mot2m = 12;      //                 CLOSING

int mot3p = 10;      // Motor 3  RING   OPENING  sensor 3
int mot3m = 11;      //                 CLOSING

int mot4p = 5;       // Motor 4  PINKY  OPENING
int mot4m = 4;       //                 CLOSING

int BIN_1 = 9;       // Motor 5  AXIS
int BIN_2 = 8;

int AIN_1 = 3;       // Motor 6  JOINT 
int AIN_2 = 2;

int sensorValue1 = 0;  // variable to store the value coming from the sensor
int sensorValue2 = 0;
int sensorValue3 = 0;

void setup() {
  Wire.begin();
  Serial.begin(9600);

//  Setpoint = 75;
//  myPID.SetMode(AUTOMATIC);
//  myPID.SetTuning(Kp, Ki, Kd);
 
  
  pinMode(mot1p, OUTPUT);
  pinMode(mot1m, OUTPUT);
  pinMode(mot2p, OUTPUT);
  pinMode(mot2m, OUTPUT);
  pinMode(mot3p, OUTPUT);
  pinMode(mot3m, OUTPUT);
  pinMode(mot4p, OUTPUT);
  pinMode(mot4m, OUTPUT);
  
  pinMode(AIN_1, OUTPUT);
  pinMode(AIN_2, OUTPUT);
  pinMode(BIN_1, OUTPUT);
  pinMode(BIN_2, OUTPUT);
  pinMode(encoder0PinA, INPUT);
  pinMode(encoder0PinB, INPUT);
  pinMode(encoder1PinA, INPUT);
  pinMode(encoder1PinB, INPUT);
}

void Read1(){
 // encoderPosR = encoderPos;
  
  n0 = digitalRead(encoder0PinA);
  if ((encoder0PinALastR == LOW) && (n0 == HIGH)) {
    if (digitalRead(encoder0PinB) == LOW) {
      encoder0PosR--;
    } else {
      encoder0PosR++;
    }
    //pos0 = encoder0PosR;
    Serial.print (encoder0PosR);
    Serial.print ("\n");
    //encoder0Pos = encoder0PosR;
  }
  encoder0PinALastR = n0;
 }


void Read2(){
 // encoderPosR = encoderPos;
  
  n1 = digitalRead(encoder1PinA);
  if ((encoder1PinALastR == LOW) && (n1 == HIGH)) {
    if (digitalRead(encoder1PinB) == LOW) {
      encoder1PosR--;
    } else {
      encoder1PosR++;
    }
   // pos1 = encoder1PosR;
    Serial.print (encoder1PosR);
    Serial.print ("\n");
    //encoder1Pos = encoder1PosR;
  }
  encoder1PinALastR = n1;
 }


void loop() {
// Read1();
// Read2();
 sensorValue1 = analogRead(sensorPin1);
 sensorValue2 = analogRead(sensorPin2);
 sensorValue3 = analogRead(sensorPin3);


     if(sensorValue1<20 && sensorValue1>330){
      digitalWrite(mot1p, LOW);
      digitalWrite(mot1m, LOW);      
     }else if((rotateVal1-sensorValue1)>=-5 && (rotateVal1-sensorValue1)<=5 ){
      digitalWrite(mot1p, LOW);
      digitalWrite(mot1m, LOW);
     }else if (rotateVal1>sensorValue1){
      digitalWrite(mot1p, HIGH); //OPENS INDEX finger
      digitalWrite(mot1m, LOW);              
     }else if(rotateVal1<sensorValue1){
      digitalWrite(mot1p, LOW); //CLOSES INDEX finger
      digitalWrite(mot1m, HIGH);  
     }
     
     if(sensorValue2<20 && sensorValue2>330){
      digitalWrite(mot2p, LOW);
      digitalWrite(mot2m, LOW);      
     }else if((rotateVal2-sensorValue2)>=-5 && (rotateVal2-sensorValue2)<=5 ){
      digitalWrite(mot2p, LOW);
      digitalWrite(mot2m, LOW);
     }else if (rotateVal2>sensorValue2){
      digitalWrite(mot2p, HIGH); //OPENS MIDDLE finger
      digitalWrite(mot2m, LOW);              
     }else if(rotateVal2<sensorValue2){
      digitalWrite(mot2p, LOW); //CLOSES MIDDLE finger
      digitalWrite(mot2m, HIGH);  
     } 
     
     if(sensorValue3<20 && sensorValue3>330){
      digitalWrite(mot3p, LOW);
      digitalWrite(mot3m, LOW);
      digitalWrite(mot4p, LOW);
      digitalWrite(mot4m, LOW);  
     }else if((rotateVal3-sensorValue3)>=-5 && (rotateVal3-sensorValue3)<=5 ){
      digitalWrite(mot3p, LOW);
      digitalWrite(mot3m, LOW);
      digitalWrite(mot4p, LOW);
      digitalWrite(mot4m, LOW);
     }else if (rotateVal3>sensorValue3){
      digitalWrite(mot3p, HIGH); //OPENS RING finger
      digitalWrite(mot3m, LOW);
      digitalWrite(mot4p, HIGH); //OPENS PINKY
      digitalWrite(mot4m, LOW);                  
     }else if(rotateVal3<sensorValue3){
      digitalWrite(mot3p, LOW); //CLOSES RING finger
      digitalWrite(mot3m, HIGH);
      digitalWrite(mot4p, LOW); //CLOSES PINKY
      digitalWrite(mot4m, HIGH);  
     }else{
      digitalWrite(mot1p, LOW);
      digitalWrite(mot1m, LOW);
      digitalWrite(mot2p, LOW);
      digitalWrite(mot2m, LOW);
      digitalWrite(mot3p, LOW);
      digitalWrite(mot3m, LOW);
      digitalWrite(mot4p, LOW);
      digitalWrite(mot4m, LOW);      
     }
     
//int mSpeed1 = 160;                                  // speed of the AXIS MOTOR
//
// if((encoder0PosR-rotateVal7)>-2 && (encoder0PosR-rotateVal7)<2){              // THUMB AXIS
//  digitalWrite(BIN_1, LOW);
//  digitalWrite(BIN_2, LOW);
// }else if((encoder0PosR-rotateVal7)<20 && (encoder0PosR-rotateVal7)>0){
//  analogWrite(BIN_1, mSpeed1);
//  digitalWrite(BIN_2, LOW);
// }else if((rotateVal7-encoder0PosR)<20 && (rotateVal7-encoder0PosR)>0){
//  digitalWrite(BIN_1, LOW);
//  analogWrite(BIN_2, mSpeed1);
// }else if(encoder0PosR < rotateVal7){
//  digitalWrite(BIN_1, LOW);
//  analogWrite(BIN_2, mSpeed1);
// }else if(encoder0PosR > rotateVal7){
//  analogWrite(BIN_1, mSpeed1);
//  digitalWrite(BIN_2, LOW);
// }
//
// int mSpeed2 = 160;                                 // speed of the JOINT MOTOR
// 
// if((encoder1PosR-rotateVal8)>-2 && (encoder1PosR-rotateVal8)<2){              // THUMB JOINT
//  digitalWrite(AIN_1, LOW);
//  digitalWrite(AIN_2, LOW);
// }else if((encoder1PosR-rotateVal8)<20 && (encoder1PosR-rotateVal8)>0){
//  digitalWrite(AIN_1, LOW);
//  analogWrite(AIN_2, mSpeed2);
// }else if((rotateVal8-encoder1PosR)<20 && (rotateVal8-encoder1PosR)>0){
//  analogWrite(AIN_1, mSpeed2);
//  digitalWrite(AIN_2, LOW);
// }else if(encoder1PosR < rotateVal8){
//  analogWrite(AIN_1, mSpeed2);
//  digitalWrite(AIN_2, LOW);
// }else if(encoder1PosR > rotateVal8){
//  digitalWrite(AIN_1, LOW);
//  analogWrite(AIN_2, mSpeed2);
// }
 
 if (Serial.available() > 0){
  serialRead();
  switch(serialData)
   {
    case 1:
      { serialRead();
        rotateVal1 = serialData;
        Serial.print("Value of sensor:  ");
        Serial.print(sensorValue1);
        Serial.print("\n");
        Serial.print("Value of rotation Point finger:  ");
        Serial.print(rotateVal1);
        Serial.print("\n");
        break;
      }
    case 2:
      {
        serialRead();
        rotateVal2 = serialData;
        Serial.print("Value of sensor:  ");
        Serial.print(sensorValue2);
        Serial.print("\n");
        Serial.print("Value of rotation Middle finger:  ");
        Serial.print(rotateVal2);
        Serial.print("\n");
        break;
      }
    case 3:
      {
        serialRead();
        rotateVal3 = serialData;
        Serial.print("Value of sensor:  ");
        Serial.print(sensorValue3);
        Serial.print("\n");
        Serial.print("Value of rotation Ring finger:  ");
        Serial.print(rotateVal3);
        Serial.print("\n");
        break;
      }
    case 4:
      { 
        serialRead();
        rotateVal7 = serialData;
        x = serialData; 
        Wire.beginTransmission(9); // transmit to device #9
        Wire.write("a");
        Wire.write(x);              // sends x 
        Wire.endTransmission();    // stop transmitting
           
        Serial.print("Value of rotation thumb:  ");
        Serial.print(rotateVal7);
        Serial.print("\n");
        break;        
      }
    case 5:
      { serialRead();
        rotateVal8 = serialData;
        x = serialData; 
        Wire.beginTransmission(9); // transmit to device #9
        Wire.write("b");
        Wire.write(x);              // sends x 
        Wire.endTransmission();    // stop transmitting
        
        Serial.print("Value of rotation joint:  ");
        Serial.print(rotateVal8);
        Serial.print("\n");
        break;
      }
     case 6: 
      {
        digitalWrite(AIN_1, LOW);
        digitalWrite(AIN_2, LOW);
        digitalWrite(BIN_1, LOW);
        digitalWrite(BIN_2, LOW);
        digitalWrite(mot1p, LOW);
        digitalWrite(mot1m, LOW);
        digitalWrite(mot2p, LOW);
        digitalWrite(mot2m, LOW);
        digitalWrite(mot3p, LOW);
        digitalWrite(mot3m, LOW);
        digitalWrite(mot4p, LOW);
        digitalWrite(mot4m, LOW);
        
 
        Wire.beginTransmission(9); // transmit to device #9
        Wire.write("c");          // sends x 
        Wire.endTransmission(); 
        rotateVal1 = sensorValue1;
        rotateVal2 = sensorValue2;
        rotateVal3 = sensorValue3;
        delay(1000);               
        Serial.print("Command of STOP");
        Serial.print("\n");
        break;                         
      }      
    case 7:
      {
        Serial.print("S1: ");
        Serial.print(sensorValue1 );
        Serial.print("\t");    
      
        Serial.print("  S2: ");
        Serial.print(sensorValue2);
        Serial.print("\t");
      
        Serial.print("S3: "); 
        Serial.print(sensorValue3);
        Serial.print("\t"); 

        Serial.print("  inVal1: "); 
        Serial.print(rotateVal1);
        Serial.print("\t");
        
        Serial.print("inVal2: "); 
        Serial.print(rotateVal2);
        Serial.print("\t");

        Serial.print("inVal3: "); 
        Serial.print(rotateVal3);
        Serial.print("\n");

        Serial.print("Value of pos Axis:  ");
        Serial.print(encoder0PosR);
        Serial.print("\t");
        Serial.print("\t");
        Serial.print("Value of pos JOINT:  ");
        Serial.print(encoder1PosR);
        Serial.print("\n");
        break;
      } 
    case 8:
      {
        digitalWrite(AIN_1, LOW);
        digitalWrite(AIN_2, LOW);
        digitalWrite(BIN_1, LOW);
        digitalWrite(BIN_2, LOW);
        delay(100);
        encoder0PosR = 0;
        encoder1PosR = 0;
        rotateVal7 = 0;
        rotateVal8 = 0;           
        break;
      }     
   }     
 }
}


long getSerial()
{
  serialData = 0;
  while (inbyte != '/')
  {
    inbyte = Serial.read();
    if (inbyte > 0 && inbyte != '/')
    {
      serialData = serialData * 10 + inbyte - '0';  
      Serial.println(serialData);
    }
  }
  inbyte = 0; 
  return serialData;

}


long serialRead()
{
  serialData = 0;
  while (inbyte != '/')
  {
    inbyte = Serial.read();
    if (inbyte > 0 && inbyte != '/')
    {
      serialData = serialData * 10 + inbyte - '0';  
      Serial.println(serialData);
    }
  }
  inbyte = 0; 
  return serialData;
}

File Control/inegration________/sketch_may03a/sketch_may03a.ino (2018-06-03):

#include <PID_v1.h>

//#define enc_th  A6 //thumb 
#define enc_p  A10 //pointing
#define enc_m  A9 //middle
#define enc_r  A8 //ring
#define enc_l  A7 //little
//#define enc_th_s  A11 //thumb  side

int encoder0PinA = 36;
int encoder0PinB = 40;
int encoder0Pos = 0;
int encoder0PinALast = LOW;
int n0 = LOW;
long pos0 = 0;

int encoder1PinA = 24;
int encoder1PinB = 28;
int encoder1Pos = 0;
int encoder1PinALast = LOW;
int n1 = LOW;
long pos1 = 0;
int encoderPinALastR = 0;

int encoderPosR = 0;


//const int initB = {13};

const int FLEX_PINs[] = {A0, A1, A2, A4};//thumb, pointing, middle, thumb side
int pinCount = 4;
//int input, output; //for PID
double Setpoint, input, output;
int init_glove[] = {283, 300, 178, 415};//thumb, point middle thumb side
int fin_glove[] = {306, 510, 390, 445};
PID myPID(&input, &output, &Setpoint, 2, 1, 1, DIRECT);

void setup() {
  Serial.begin(9600);
 // pinMode(enc_th, INPUT);
 long pos0 = 0;
  pinMode(enc_p, INPUT);
  pinMode(enc_m, INPUT);
  pinMode(enc_r, INPUT);
  pinMode(enc_l, INPUT);
 // pinMode(enc_th_s, INPUT);

  pinMode(encoder0PinA, INPUT);
  pinMode(encoder0PinB, INPUT);
  pinMode(encoder1PinA, INPUT);
  pinMode(encoder1PinB, INPUT);


  Setpoint = 1;

  // pinMode(initB, INPUT);

  pinMode(4, OUTPUT);
  pinMode(5, OUTPUT);
  pinMode(6, OUTPUT);
  pinMode(7, OUTPUT);
  pinMode(8, OUTPUT);
  pinMode(9, OUTPUT);
  pinMode(10, OUTPUT);
  pinMode(11, OUTPUT);

  myPID.SetMode(AUTOMATIC);
  for (int thisPin = 0; thisPin < pinCount; thisPin++) {
    pinMode(FLEX_PINs[thisPin], INPUT);
  }

}

void Read(int n, int encoderPinA, int encoderPinB, int encoderPos){
 // encoderPosR = encoderPos;
  
  n = digitalRead(encoderPinA);
  if ((encoderPinALastR == LOW) && (n == HIGH)) {
    if (digitalRead(encoderPinB) == LOW) {
      encoderPosR--;
    } else {
      encoderPosR++;
    }
    pos0 = encoderPosR;
   // Serial.print (encoderPosR);
    //Serial.print ("\n");
    encoderPos = encoderPosR;
  }
  encoderPinALastR = n;
  }



//bool initiate(){
//
//  *init_glove=readGlove();//open hand
//  delay(3000);
//  *fin_glove=readGlove();//closed hand
//
//  if (init_glove[0]!=0 && fin_glove[0]!=0 ){
//     return 1;
//     }else{
//         return 0;
//         }
//}

int saferange(int finger, int value) {
  if (finger == 2 && (value > 720 || value < 1016 )) {//
    if (value < 720) {
      value = 720;
    }
    else if (value > 1016) {
      value = 1016;
    }
    else {}
    return  map(value, 720, 1016, 0, 90);
  }
  else if (finger == 3 && (value > 750 || value < 1006 )) {
    if (value < 720) {
      value = 720;
    }
    else if (value > 1006) {
      value = 1006;
    }
    else {}
    return map(value, 750, 1023, 0, 90);
  }
  //  else if (finger == 4 && (value > 750 || value < 1023 )) {
  //    if (value < 720) {
  //      value = 720;
  //    }
  //    else if (value > 1016) {
  //      value = 1016;
  //    }
  //    else {}
  //    return map(value, 750, 1023, 0, 90);
  //  }
  else if (finger == 5 && (value > 5 || value < 260 )) {
    if (value < 750) {
      value = 750;
    }
    else if (value > 1023) {
      value = 1023;
    }
    else {}
    value = 1000 - value;
    return map(value, 750, 1023, 0, 90);
  }
  else if (finger == 0 && (value > 0 || value < 20 )) {//thumb
    if (value < 0) {
      value = 0;
    }
    else if (value > 20) {
      value = 20;
    }
    else {}
    // return map(value, 0, 40, 0, 90);
    return value;
  }
  else if (finger == 1 && (value > 0 || value < 20 )) {
    if (value < 0) {
      value = 0;
    }
    else if (value > 20) {
      value = 20;
    }
    else {}
    return map(value, 0, 20, 0, 20);
  }
  else {
    return 0;
  }
}

void motor (int finger, int toClose, int pwm) {
  if (toClose == 1) { //close
    analogWrite(finger * 2, pwm);
    analogWrite((finger * 2 + 1), 0);
  }
  else if (toClose == 0) { //open
    analogWrite(finger * 2 + 1, pwm);
    analogWrite((finger * 2), 0);
  }
  else { //stop
    analogWrite(finger * 2 + 1, 0);
    analogWrite((finger * 2), 0);
  }
}



void direction(int enc, int ref, int finger) {

  double pwm = 0;
  
  if (enc > 0 || enc==0) {
    int diff = 0;
    diff = ref - enc;
    input = diff;
    myPID.Compute();
  //Serial.println("Inside the direction " + String(diff));
    //Serial.println(String(diff)+" diff");
    //Serial.println(String(output)+" output");
    pwm = map(output, 0, 255, 190, 250 );
    //  Serial.println(String(output) + " PID");
    if (diff > 10) {
      Serial.println("closing finger " + String(finger));
      motor(finger, 1, pwm);//to close
      delay(1);
    } else if (diff < -10) {
      Serial.println("openning finger " + String(finger));
      motor(finger, 0, pwm); //to open
      delay(1);
    } else {
      Serial.println("Stopped finger " + String(finger));
      motor(finger, 2, 150);//to stop
      delay(1);
    }
  } else {
    motor(finger, 2, 0);
  }
}


void loop() {
  int ready = 0;

  // if (digitalRead(initB)==HIGH){
  //   ready=initiate();
  //  Serial.println("Ready! You can start");
  //}
  //  if (ready==1){
  int ref[6];

  int flex[] = {0, 0, 0, 0};
  for (int thisPin = 0; thisPin < pinCount; thisPin++) {
    if (thisPin == 3) {
      flex[thisPin] = analogRead(FLEX_PINs[thisPin]);
    }
    else
    { flex[thisPin] = 1000 - analogRead(FLEX_PINs[thisPin]);
    }

    //Serial.print(" [" + String(init_glove[thisPin]) + "  " + String(flex[thisPin]) + "  " + String(fin_glove[thisPin]) + "] ");
    if (flex[thisPin] < init_glove[thisPin] ) {
      flex[thisPin] = init_glove[thisPin];
    }
    if (flex[thisPin] > fin_glove[thisPin] ) {
      flex[thisPin] = fin_glove[thisPin];
    }
    if (thisPin == 0) {

      ref[thisPin] = map(flex[thisPin], init_glove[thisPin], fin_glove[thisPin], 0, 20);
    }
    else if (thisPin==3){
      ref[thisPin] = map(flex[thisPin], init_glove[thisPin], fin_glove[thisPin], 0, 20);
      }
    else {
      ref[thisPin] = map(flex[thisPin], init_glove[thisPin], fin_glove[thisPin], 0, 90);
    }
  }
  ref[5] = ref[3];
  ref[3] = ref[2];
  ref[4] = ref[2];

Read(n0, encoder0PinA, encoder0PinB, encoder0Pos);
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

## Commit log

2018-06-03 CAD files
    [1 DOF Thumb.SLDPRT, 12teeth.SLDPRT, 13_teeth.SLDPRT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]
2018-06-03 Code for Arduino
2018-06-17 Add files via upload
    Housing for PCB and Arduino
    [Assem1.SLDASM, Part1.SLDPRT, Part2.SLDPRT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]
2018-06-25 Add files via upload
    serial communication with arduino through serial monitor
2018-06-28 Add files via upload
    control motors with encoders through serial monitor
2018-06-28 Add files via upload
    full hand control with thumb and fingers
2018-06-28 Add files via upload
    Housing for arduino and motor shield
    [Assem1.SLDASM, Part1.SLDPRT, Part2.SLDPRT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]
2018-07-23 Add files via upload
    CAD files for adaptive finger mechanism
    [Assem2.SLDASM, Finger Base.SLDPRT, Finger Base.STL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]
2018-08-01 Improved version of finger mechanism with rails
    [298,1 Micro Metal Gearmotor MP.SLDPRT, Assem1.SLDASM, Back_hand.SLDASM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]
2018-08-15 Add files via upload
    Rail mechanism
2021-05-28 stl in ascii
